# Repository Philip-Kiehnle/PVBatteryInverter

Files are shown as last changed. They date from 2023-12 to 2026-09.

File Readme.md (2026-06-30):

# PVBatteryInverter - Highly Efficient Photovoltaic and Battery Hybrid Inverter using GaN Semiconductors
This project was inspired by multiple drivers:
 * AC-connected battery systems have disadvantages in terms of charging efficiency ( PV -> DC/AC -> AC/DC -> Battery ) and cost/environmental impact, because of the additional inverter.  
 A multilevel battery converter is efficient but does not offer a DC port for PV and thus, increases installed converter power in the grid and grid operators have to calculate the worst case for grid utilization.
 * DC-connected battery systems do not guarantee a better efficiency by default. E.g. in case of a large inverter (~10 kW) operating under small loads during nighttime (30–150 Watt).
 * Commercial solutions often require an additional power meter for the self-consumption power control. In my opinion, this is a complete waste of time, space, resources and energy:
   * The installation is complicated, and requires space in the meter cabinet.
   * The additional power meter requires extra power of 0.4–2 Watt.
   * The additional power meter has an offset from the official meter measurement, meaning it cannot be used for exact zero-import control.
   * The digital energy meters in Germany already offer an optical interface, which can be set to send the actual power every second  [More details below](#head_electricityMeter)
 * GaN instead of SiC or Si-IGBT offers improved efficiency.
 * No GaN-based inverter is out there at the moment (9.12.2023)
 * Second-life 6 kWh battery was available
 * GaN full-bridge cells were available from another project
 * New west oriented PV plant has some shaded areas, which are directly connected to microinverter. But 8 PV-modules are unshaded most of the time and require a string inverter. A Hybrid (PV+Battery) Inverter for the unshaded PV-modules and a microinverter for the shaded PV-modules looks like the optimal solution.

Let's build an efficient 2kW hybrid inverter, which solves all the problems shown above!

System Overview:

System Overview

# Components

## PV Plant
```
8 x 405 W PV-modules in the string
STC:
Vmpp_module(25°C) = 36.48 V
Impp_module(25°C) = 11.10 A
Voc_module(25°C)  = 46.30 V

Temperature Coefficients of Voc = -0.28 %
Voc_module(-15°C)  = 51.49 V
Voc_string(-15°C)  = 411.9 V -> 650 V GaN semiconductors
```

## High-Voltage Battery
```
nunm_cells = 96
Vmin = 96 * 3.3 V = 316.8 V (grid feed-in is only possible when grid rms voltage is below 224 V or by using reactive power)
Vnom = 96 * 3.7 V = 355.2 V
Vmax = 96 * 4.2 V = 403.2 V
energy = 18 Ah * 355.2 V = 6.4 kWh
```

## Inverter Housing
An unused inverter housing was available, including passive components like boost inductors and an LCL-filter, which can be reused.

A control PCB and GaN Full-Bridge PCBs were added. This picture was taken during the development phase:

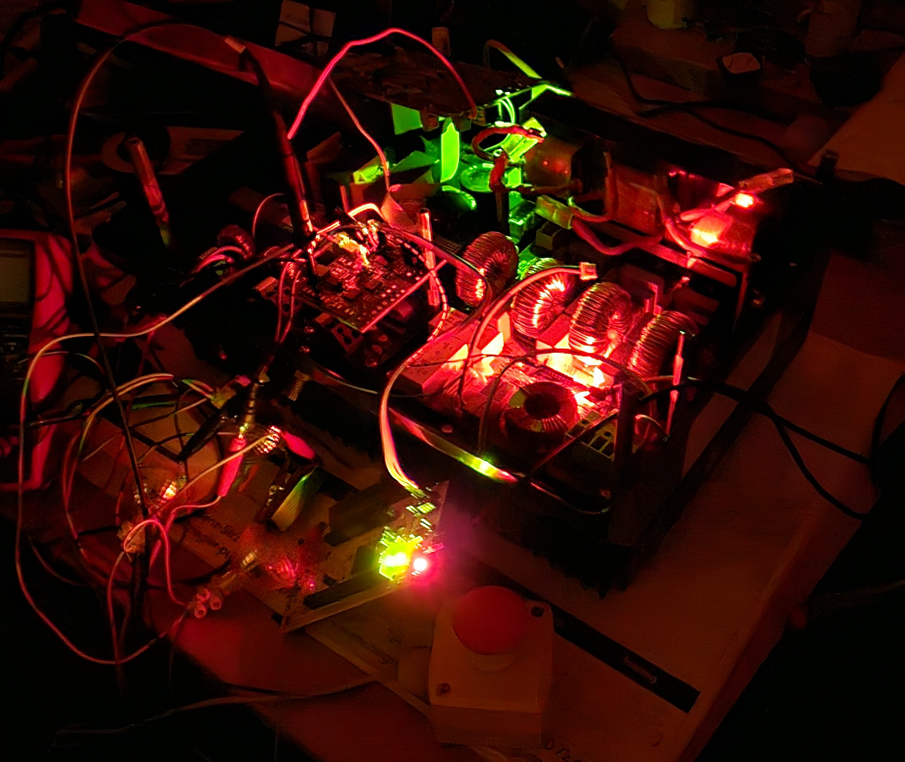
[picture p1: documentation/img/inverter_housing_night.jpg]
Inverter Housing


### PV input
Common-Mode-Choke (CMC) -> Capacitor: MKP 900V  12.5uF +-5% -> Inductor -> Diode for PV string protection during development -> GaN Half-Bridge

### LCL-Filter
Inverter side inductor: 1mH

### GaN Full-Bridge
```
GaN semiconductors:
Gan Systems GS66508B 650 V
Rds_on(25°C)  =  50 mOhm
Rds_on(112°C) = 100 mOhm

estimated loss:
I = 2000 W ÷ 230 V = 8.7 A
50 % conduction of low and high-side switch
Pcond(112°C) = 0.5*0.1 Ohm*(8.7 A)^2 = 3.8 W per switch

Switching loss (according to datasheet at Vds = 400 V, Ids = 15 A):
Eon=47.5 µJ
Eoff=8 µJ
Pswitch = 20 kHz * (47.5+8) µJ = 1.1 W
-> 4.9 W have to be dissipated for each transistor 

Thermal Model:
R_JC = 0.5 K/W (manufacturer)
R_PCB = 3.39 K/W
R_TIM = 0.28 K/W
R_HSA = 4.8 K/W
R= 8.97 K/W
Thermal interface material coefficient seems too optimistic -> use R=10K/W
With ambient 40°C and junction = 112°C each transistor can dissipate P=(112-40)/10=7.2W
This assumption has enough tolerance because:
  -operating junction temperature is 150°C and not 112°C
  -dissipated power will be lower than 7.2W

If the power rating is set to 2300 W, the loss will increase to:
Ploss = Pswitch + 0.5*0.1 Ohm*(10 A)^2 = 1.1 W + 5 W = 6.1 W
But the inverter's inductors had an original design power of 2 kW. On the other hand, the ripple is lower than in the original design, because of an increased switching frequency.
This increases the core loss but the central inductor of phase L2 can be assumed as a heat sink, because it is not used.

Start heatsink fan at 1200W (5.2A) assume 90mOhm:
Ploss = Pswitch + 0.5*0.09 Ohm*(5.2 A)^2 = 1.1 W + 1.2 W = 2.3 W
Minimum runtime is 30 sec, stop if power after timer runtime is lower than 1 kW. Restart timer if power > 1.2 kW during fan runtime.
```

### Control board [PVBatteryInverter_Mainboard](PVBatteryInverter_Mainboard)
An STM32G474 microcontroller is used to control the system.

#### Code Execution:

HRTIM 20 kHz controls Grid Full-Bridge
1. HRTIM period triggers ADC1
2. ADC1 DMA done calls ADC_ConvComplete with hadc1 instance
3. ADC2 for PV current is started (two ADCs simultaneously cause disturbance!)
4. AC control algorithm is executed and new dutycycle is set
5. 45 µs after ADC2 start, the 128 PV/DC current samples are acquired and ADC DMA calls ADC_ConvComplete with hadc2 instance
6. DC control algorithm is executed and new dutycycle is set. Exact timing not relevant for slow MPP-Tracker
7. wait for new ADC1 samples

## Energy Management System
Todo: opensource the git repo and add link

## Default Electricity Meter

The Iskra electricity meter offers a power resolution of 1 Watt and a temporal resolution of 1 second.  
Its permanent energy counting registers are written every 100 mWh.  
This equals to a power mismatch of 360 W for 1 second.  
So the controller has to avoid that, which is possible most of the time.  
In case of large load steps, like hobs switching with 2 kW, there will be a mismatch.  
But experiments have shown that for a cooking session of 30 minutes, a mismatch of about 12 Wh occurs.  
If this amount is equally spread over 24 hours, the mismatch in each hour is 0.5 W.
To beat that value, an additional energy meter must:
  * consume less than 0.5 W
  * offer better temporal resolution than 1 second
  * offer no offset compared to the main electricity meter, or use an offset in feed-in direction and thus always feeds a little bit of power into the grid
  * come at no cost

This demonstrates the whole extent of stupidity to install an additional energy meter, if a digital electricity meter is already installed!  
A detailed analysis is also carried out in the [PowerSensorEmulator
](https://github.com/Philip-Kiehnle/PowerSensorEmulator
) repository.

# Efficiency

## Power Consumption
Assuming 90 % efficiency of the 5 V power supply.

### Mode "Connected to AC Grid - Passive"
The gate signals are turned off whenever there is no exchange of AC power.

BMS: 6 W  
Smartphone: 1 W  
PV-Boost GaN Full-Bridge not switching: 5 V ⋅ 90 mA / 0.9 = 0.5 W  
Grid GaN Full-Bridge not switching: 5 V ⋅ 90 mA / 0.9 = 0.5 W  
Grid Relay: 0.4 W  
STM32_PVBatteryInverter PCB:  5 V ⋅ 50 mA / 0.9 = 0.28 W (todo: check)  
STM32_BatterySupervisor PCB:  5 V ⋅ 40 mA / 0.9 = 0.22 W (todo: check)  

**Total: 8.9 W**

### Mode "Idle"
BMS 12 V power supply is OFF, so the idle consumption is reduced to **2.9 W**.  
The BMS reactivation and the routine for closing contactors takes about 10 seconds.

### Mode "Connected to AC Grid - Active"
Todo: measure efficiency curve

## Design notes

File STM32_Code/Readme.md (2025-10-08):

# Howto

## Bootloader

In GCC preprocessor define USE_FULL_LL_DRIVER

Enter bootloader by pressing emergency stop and the reset button.  
In bootloader both LEDs (red and green) are lit.

```
philip@792G:~/Downloads/stm32flash-0.7$ ./stm32flash /dev/ttyUSB1 -b 115200
stm32flash 0.7

http://stm32flash.sourceforge.net/

Interface serial_posix: 115200 8E1
Version      : 0x31
Option 1     : 0x00
Option 2     : 0x00
Device ID    : 0x0469 (STM32G47xxx/48xxx)
- RAM        : Up to 96KiB  (16384b reserved by bootloader)
- Flash      : Up to 512KiB (size first sector: 1x2048)
- Option RAM : 48b
- System RAM : 28KiB

```

Write with verify and start application:
```
./stm32flash -b 115200 -w firmware.bin -v -g 0x8008000 -S 0x8008000 /dev/ttyUSB1
```
If process is interrupted, the booloader recovers after some minutes and the flash application can be restarted. 

Or flash via Android phone:
```
adb -e push 'STM32_PVBatteryInverter/Debug/STM32_PVBatteryInverter.bin' /data/local
adb -e shell
pkill log-
/data/local/stm32flash -b 115200 -w /data/local/STM32_PVBatteryInverter.bin  -v -g 0x8008000 -S 0x8008000 /dev/ttyUSB1
# A reset seems to be necessary after flash process. Direct start does not charge battery.
```

### Problems:
#### Data corruption can lead to execution of incomplete program
Todo: protect flash of bootloader and implement CRC (in bootloader seems more robust than in image. Bootloader should check CRC before starting the application.)

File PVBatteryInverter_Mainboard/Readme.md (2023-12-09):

# Aisler PCB made in Germany
minium amount: 3pcs  
area: 100mm*60mm = 60cm²  
```
Price Budget 2-Layer: 10€ + 3* 60*0.0525€/cm² = 19,45€ -> 23,15€
Price HD 2-Layer:     12€ + 3* 60*0.084€/cm²  = 27,12€ -> 32,27€
Price HD 4-Layer:     12€ + 3* 60*0.117€/cm²  = 33,06€ -> 39,34€
```

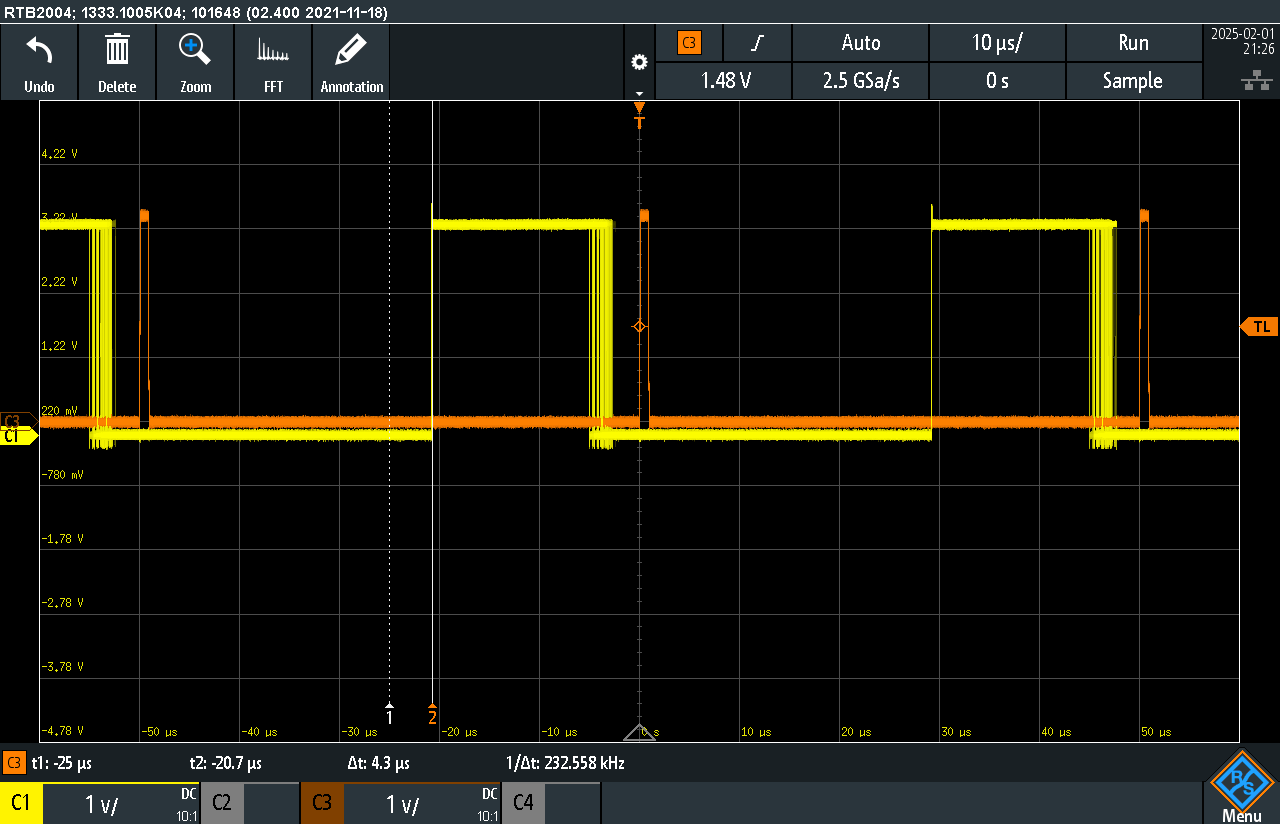
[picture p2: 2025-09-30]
documentation/img/4XOSR_ADC_delay.PNG

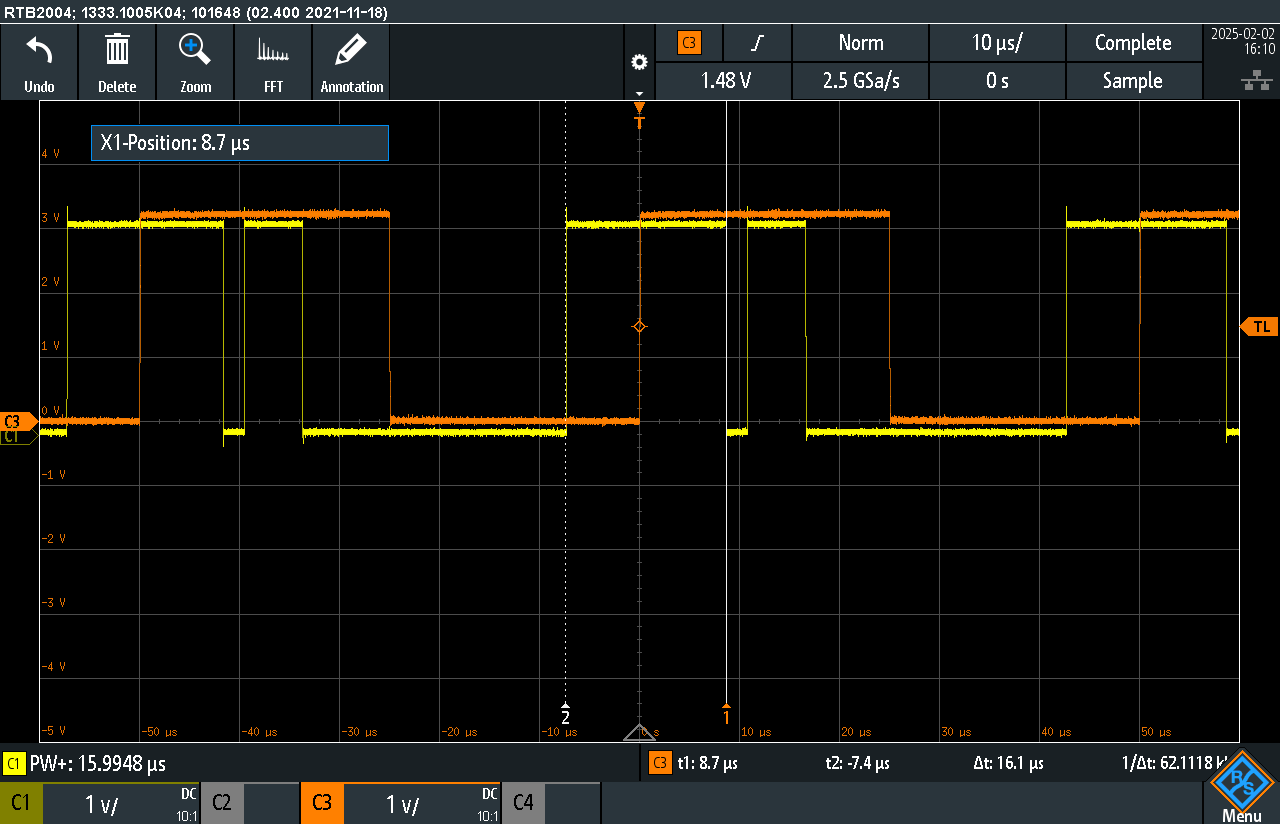
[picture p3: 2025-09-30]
documentation/img/2_phase_correct_ADC_trig_8xOSR_AC_ctrl.PNG

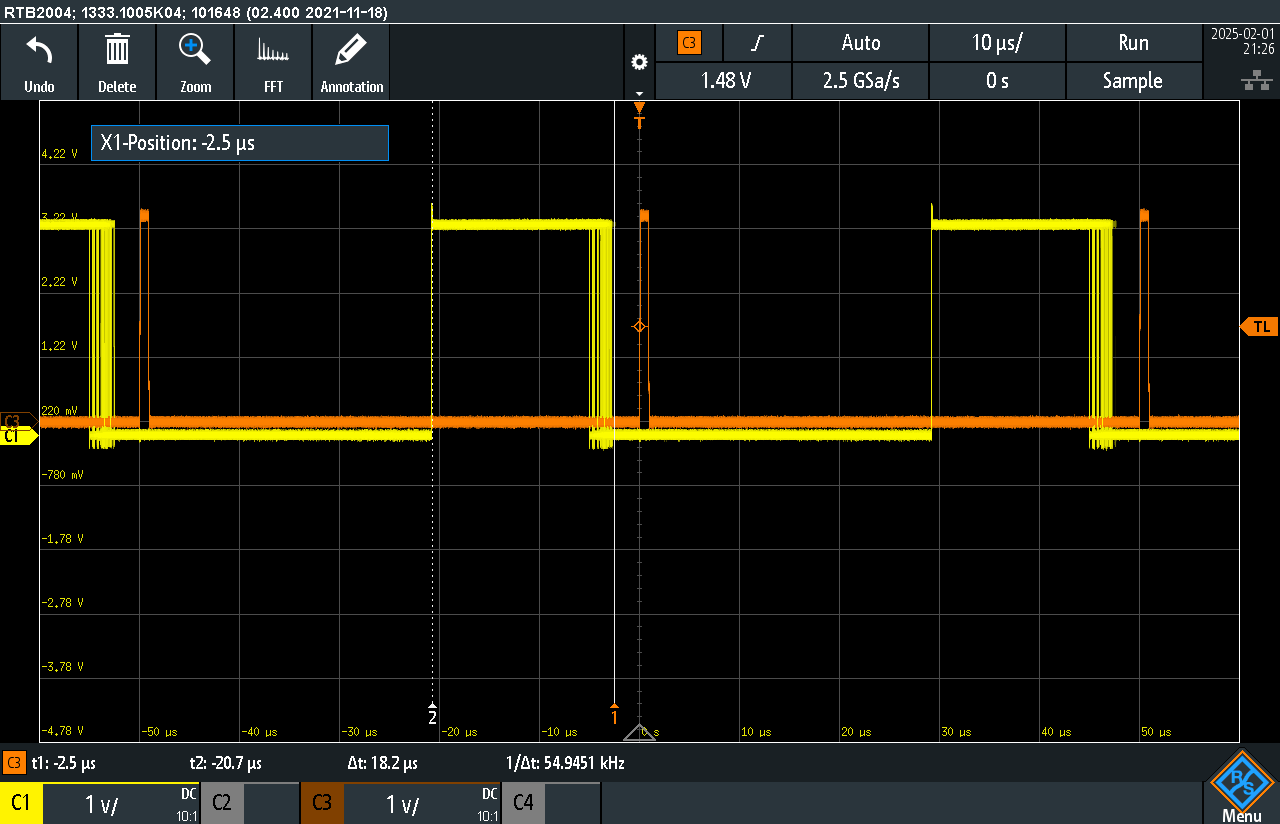
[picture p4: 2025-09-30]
documentation/img/4XOSR_ac_duty_calc_duration.PNG

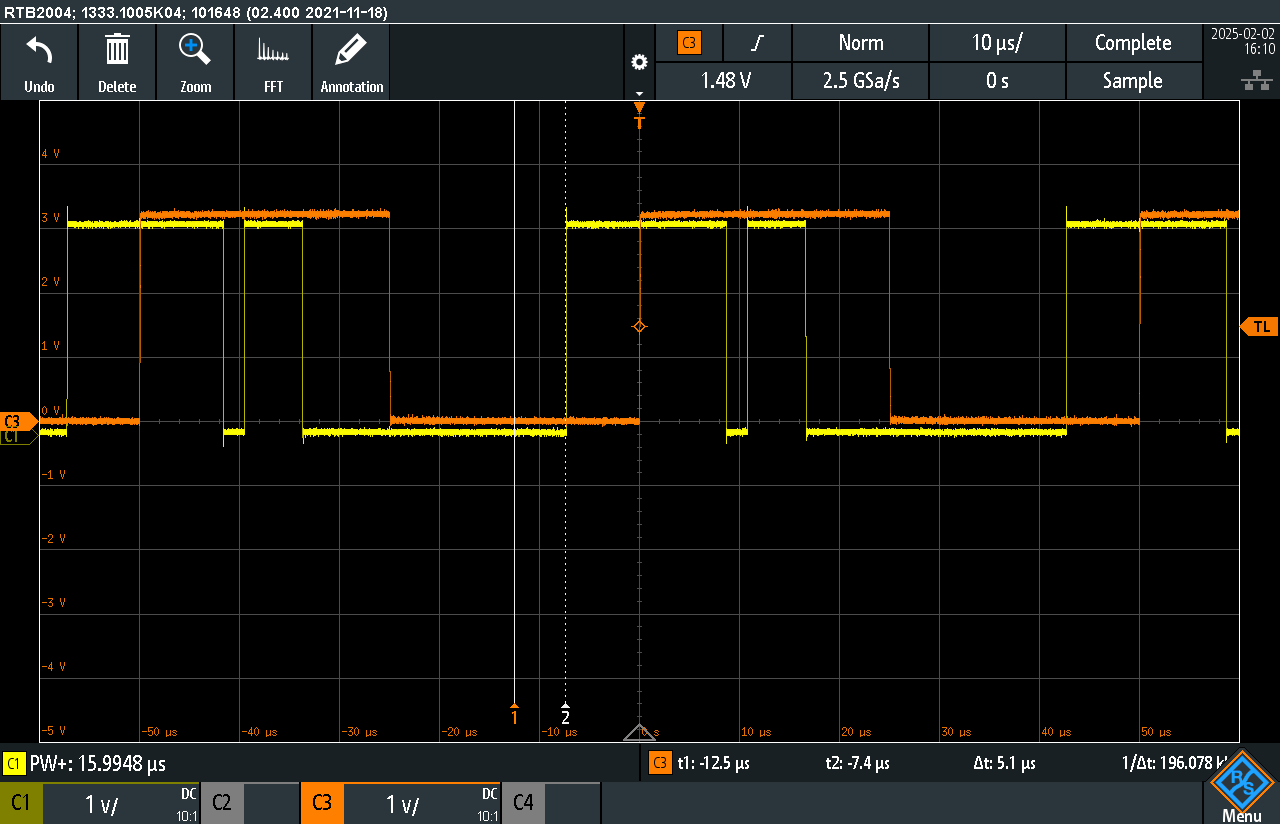
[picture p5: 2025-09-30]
documentation/img/1_phase_correct_ADC_trig_8xOSR_delay_until_ISR_start.PNG

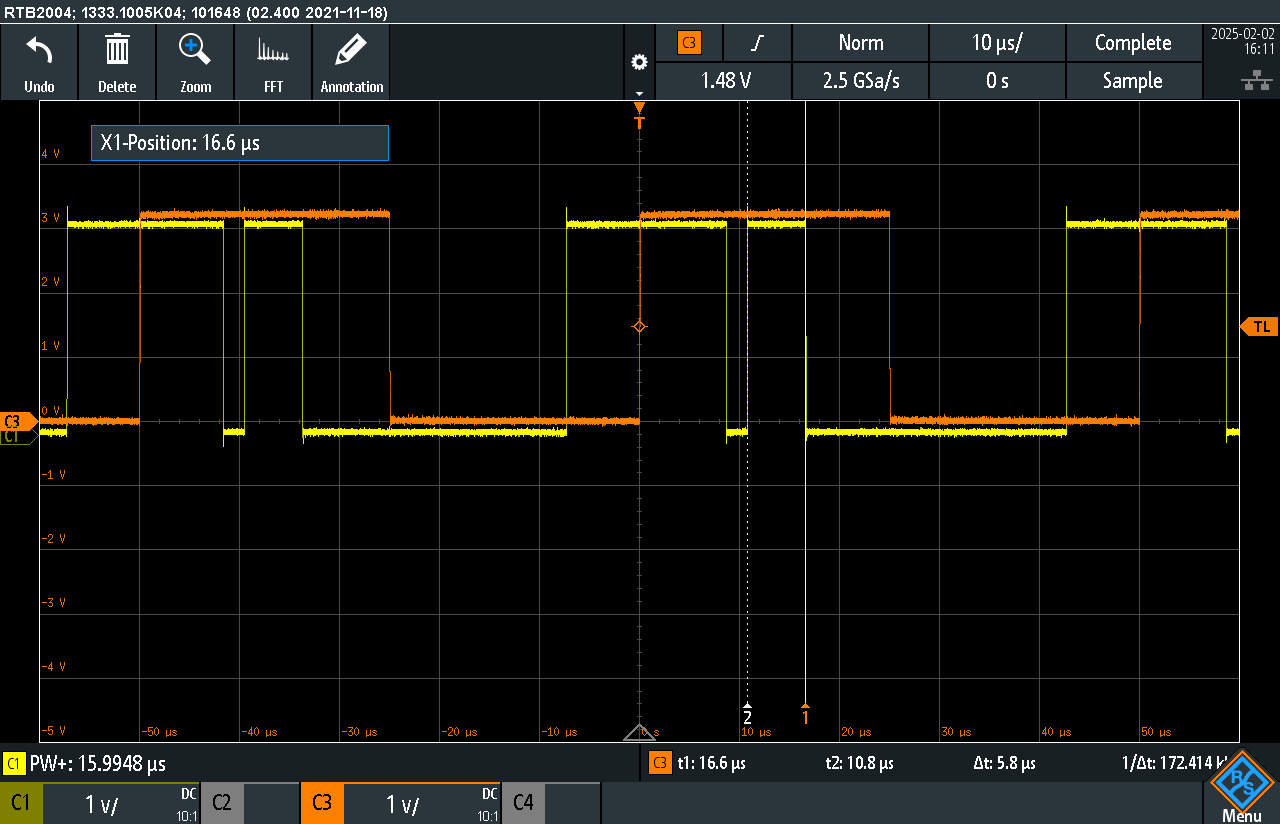
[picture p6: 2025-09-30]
documentation/img/4_phase_correct_ADC_trig_8xOSR_DC_ctrl.PNG

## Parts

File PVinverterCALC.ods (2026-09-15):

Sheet: Tabelle1
P | 75 | W
U | 230 | V
R | 705,333333333333 | Ohm
R | 400 | Ohm |  |  | 190 |  |  | 10,6 |  |  | 22
U | 38 | V |  | 450 |  |  | 33 |  |  | 33
I | 0,095 | A |  |  | 0,421286031042129 |  |  | 0,311764705882353 |  |  | 0,647058823529412
P | 3,61 | W |  | 1 |  |  | 1 |  |  | 1
Uin | 19 | V
Rin | 4,11 | Ohm |  | 20Watt | 7,2
I_short | 4,62 | A |  | 20Watt | 7,2
P_short | 87,83 | W |  | R | 5,6 |  | 35Watt | 4,11
 |  |  |  | 50Watt | 2,88
U0gan | 4,7 |  |  | R | 10
U0diode | 0,7 |  |  | R_ges | 32,88
Udrop | 5,4
U0 | 13,6 |  |  | P | 14,7201946472019
I0 | 0,37
Pgan | 1,73
P0 | 5,00
IDC_OFFSET_RAW | 2635
IDC_mV_per_LSB | 0,8056640625
IDC_mV_per_A | 35
IDC_RAW_TO_mA | 23,0189732142857
iDC_filt_raw | 2636
iDC_filt_mA | 23,0189732142857
DUTY_ABSMAX | 4250
VIN_MIN | 62
VIN_MAX | 320
VOUT_MIN | 288
VOUT_MAX | 384
DUTY_MIN | -472,222222222223
DUTY_MAX | 3563,80208333333
f | 20000
T | 0,00005
a | 4
C | 0,00078 | F
Tsigma | 0,00515
VR | 0,151456310679612
Tn | 0,0824
Kp_Vdc_real | 0,151456310679612
Ki_Vdc_real | 1,83806202281082
EXTEND_PI_VDC | 16
Kp_Vdc | 9925,84077669903
Ki_Vdc | 120459,23272693
c1 | 14041,5175213796
c2 | -14032,9997673478
ctrl->y += x * ctrl->c1 + ctrl->x_prev * ctrl->c2
x_prev | x | y | y_out
 | 0 | 0
0 | 100 | 1404151,75213796 | 21,4256553976128
100 | 100 | 1405003,52754113 | 21,4386524588186
 |  |  | fb boost
Vreal | corr boost | coor grid | vdc_filt50Hz | VdcFBboost_sinc | VdcFBgrid_sinc
33,2 | 33,220 | 33,246 | 33,5 | 33,5 | 33,7
33,18 |  |  | 33,5 | 33,7 | 33,7
33,18 |  |  | 33,5 | 34,4 | 33,7
33,1866666666667 |  |  | 33,5 |  | 33,7
avg_calib_corr |  |  | 0,990646766169154 |  | 0,984767556874382
45,65 | 45,615 | 45,578 | 46 | 46 | 46,2
45,66 |  |  | 46 | 46 | 46,2
45,67 |  |  | 46 | 46 | 46,2
45,66 |  |  | 46 |  | 46,2
 |  |  | 0,992608695652174 |  | 0,988311688311688
avg_calib_corr v1 |  |  | 0,991627730910664 |  | 0,986539622593035
VdcFBboost_sinc | 46,0
VdcFBgrid_sinc | 45,9
Vreal | 46,14
avg_calib_corr v2 |  |  | 1,00304347826087 |  | 1,00522875816993
calib |  |  | 0,994645728352566 |  | 0,991697999704628
 |  |  | theorey after calib |  |  |  | meas after calib
Vreal | vac_filt50Hz | error | after offset calib | after gain calib | error |  | Vreal | after calib | error
-50,48 | -50,200 |  |  |  |  |  | -50,64 | -50,5
-50,5 | -50,000 |  |  |  |  |  | -50,64 | -50,4
-50,51 | -50,200 |  |  |  |  |  | -50,63 | -50,4
-50,50 | -50,13 | 0,363 | -50,98 | -50,420 | 0,077 |  | -50,64 | -50,43 | 0,203
50,48 | 52 |  |  |  |  |  | 50,67 | 50,7
50,5 | 52 |  |  |  |  |  | 50,68 | 50,5
50,49 | 52 |  |  |  |  |  | 50,66 | 50,5
50,49 | 52,00 | 1,510 | 51,15 | 50,590 | 0,100 |  | 50,67 | 50,57 | -0,103
OFFSET | 0,933333333333351
V_AC_CALIB_OFFSET | 1976 | 3 | 1979
V_AC_CALIB_GAIN_PER_MIL | 989
VGRID_ADCR | 1157,1
ADC_BITS_VGRID | 12
vac_raw | 3,30377393523604 | 1
vac | 0,933300004995513 | 0,2824951171875
SigmaDelta software processing
single pulse edge counter
 |  |  |  | Vadc |  | edges
 |  |  |  | 0V |  | 250
 |  |  |  | 1V |  | 50
 |  |  |  | 1,25V |  | 0 | 1 in 256
Vcell |  | Vdc_max | divider | Vadc
4,25 | 96 | 408 | 0,002660 | 1,085 | 1,25 | 32,98
4,26 |  | 408,96 |  | 1,088 |  | 32,47
4,27 |  | 409,92 |  | 1,090 |  | 31,96
4,28 |  | 410,88 |  | 1,093 |  | 31,45
4,29 |  | 411,84 |  | 1,095 |  | 30,94
4,3 |  | 412,8 |  | 1,098 |  | 30,43
4,31 |  | 413,76 |  | 1,100 |  | 29,91
4,32 |  | 414,72 |  | 1,103 |  | 29,40
4,33 |  | 415,68 |  | 1,106 |  | 28,89
4,34 |  | 416,64 |  | 1,108 |  | 28,38
4,35 |  | 417,6 |  | 1,111 |  | 27,87
4,36 |  | 418,56 |  | 1,113 |  | 27,36
4,37 |  | 419,52 |  | 1,116 |  | 26,85
4,38 |  | 420,48 |  | 1,118 |  | 26,34
4,39 |  | 421,44 |  | 1,121 |  | 25,83
4,4 |  | 422,4 |  | 1,123 |  | 25,32
4,41 |  | 423,36 |  | 1,126 |  | 24,81

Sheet: Tabelle2
pll_set_phaseOffset((1<<15) * +10.0/20); // zero crossing of grid and converter voltage matched: +-1us
fgrid | 50 | Hz
R | 0,297 | Ohm
L | 0,00431 | Henry | 4,30765 | mH
ZL | 1,353 | Ohm
Z | 1,385 | Ohm
Contator OFF, Current feedforward OFF
Peak missmatch kurz nach max. Amplitude, max Verr=3,0V
Annahme: | Verr_max die ganze Zeit |  |  | realistisches Spannungsmittel über der Zeit
 | Verr | 3 | V | 2 | V
 | T_insgesamt | 1,1 | ms | 0,8 | ms
 | L | 0,002 | H | 0,002 | H
 | dI | 1,65 | A | 0,8 | A
-> kurzzeitiger Störstrom von ~1A durch nicht perfekt vorgesteuerte Netzspannung
-> Aber gut für das Netz, da damit Diodengleichrichter "ausgeglichen" werden
Contator OFF, Current feedforward ON
With I_AMP_MAX = 3,0A, Z=1,385
converter voltage leading 0,30-0324ms
Vgrid_amp | 44,53 | V
Vinv_amp | 45,61 | V
-> Vgrid_amp nur niedriger, weil Spitze abgeflacht
Vgrid_amp | -44,63 | V | -0,100000000000001
Vinv_amp | -45,61 | V | 0 | -> Spannung ist symmetrisch, Calibration hat funktioniert
Differenzspannung zwischen Netz und Inverter ca. 5,4ms = ~90° vor Netzspannung
-> Todo, nachrechnen ob die Phasenverschiebung passt

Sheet: system model
Amprobe SM-550-EUR for current measurement
UNI-T UT210E for voltage measurement
fgrid | 50 | Hz
Main Inductor
L | 2 | mH
V | 19,7 | 19,8 | 29,8 | mV
I | 293,9 | 293,8 | 441,4 | mA
R | 0,0670 | 0,0674 | 0,0675 | Ohm
R | 0,0673
Inductor 3 connection point to L3 including short N wire |  |  |  |  |  |  | Inductor 1 connection point to L1 including short L wire
V | 28,7 | 29 | 42,1 | mV | 27,7 |  | 29,2 | 28,8 | 45,1
I | 307,5 | 308 | 444 | mA | 295,5 |  | 294 | 293,6 | 448,2
R | 0,0933 | 0,0942 | 0,0948 | Ohm | 0,0937 |  | 0,0993 | 0,0981 | 0,1006
R | 0,0941 |  |  |  |  |  | 0,0993
R_out | 0,0967
L_LCL2 | 1,1 | mH without Common mode choke
Trafo | zwei serielle Windungssysteme + 5 extra Windungen mit Lüsterklemme
V | 60,6 | 92,6 | 92,4 | mV
I | 288,7 | 441,5 | 440,7 | mA
R | 0,2099 | 0,2097 | 0,2097 | Ohm
R | 0,2098
L | 30,0 | uH | 20-44uH gemessen mit rp-ims python tool am Oszi
Kupfer spez. Widerstand
 | 0,01678 | Elektrischer Widerstand Ohm mm²/m (bei 20°C)
1,5mm² | 0,01119 | Ohm/m
16mm² | 0,00105 | Ohm/m
ESR 390uF 550V ELko
340 | mΩ | 100 | Hz | 20 | °C
R_capacitor | 0 | mΩ | part of dutycycle feedback loop
Rtrack | 2 | mΩ
R_GaN | 200 | mΩ
Rtrack | 4 | mΩ
R_1u2H | 7,3 | mΩ
Rwire | 3,4 | mΩ | 15 | cm einfache Länge
R_mainL | 200,0 | mΩ
R_out | 280,5 | mΩ
R_relais | 0,1 | mΩ | Kontaktwiderstand von zwei ebenen Kupferscheiben mit D=1mm, die mit der Kraft 2,7 N aneinander gepresst werden
R_connector | 0,5 | mΩ
R_wire | 30,2 | mΩ | 135 | cm einfache Länge
R_trafo | 209,8 | mΩ | zwei serielle Windungssysteme + 5 extra Windungen
R_trafo prim | 3,4 | mΩ | 15 | m Drahtwickel | geschätzt
R_grid | 11,8 | mΩ | 7 | Winding Ratio
Rsum | 697,8 | mΩ
R_wireInHouse | 335,6 | mΩ | 15 | m einfache Länge
R_circuit_breaker | 8,5 | mΩ | ABB S200 16A B
R_fuse | 3,0 | mΩ | 35A DIIIGG50V35 |  | R_SLS_Switch | 4,6 | mΩ | Hager HTN335E
R_NHfuse | 1,2 | mΩ | 63A L223685 |  |  | 2,6 | mΩ | 35A H223682
R_wireInStreet | 209,8 | mΩ | 100 | m einfache Länge
R_MVtrafo | 20,0 | mΩ
L_track | 0,002 | mH
L_1u2H | 0,0024 | mH
L_main | 4,573 | mH
L_LCL2 | 5,614 | mH | L_LCL2 hat 496mV Spannungsabfall bei 50Hz aber L_main nur 404mV → L2 ist größer todo: warum mit rp-ims nur 1mH gemessen?
L_CMC_diff | 0,008 | mH | differential Mode inductance |  | estimated
L_wire | 0,004 | mH | Netzspannungsmessung ist Teil der feedback loop, daher ohne Berücksichtigung
L_trafo | 0,03 | mH
L_trafo_prim | 0,02 | mH | geschätzt
L_grid | 0,1 | mH | geschätzt
L_sum | 10,200 | mH |  | Ziel 10,2
R_old | 397 | mOhm | 2xGaN + 2 x large choke + 2xsmall choke + transformer
L_old | 4,308 | mHenry | 2 x large choke + 2xsmall choke (todo check 150uH) + transformer
gamma | 73,65 | °
Rsum | 697,8 | mΩ
L_sum | 10,200 | mH
R_factor | 1,76
L_factor | 2,37
Z_factor | 2,33
gamma_new | 77,72 | °
shift | 0,225834058765433 | ms
Rsum | 882,0 | mΩ | mod for more current, did not work but shifted current in phase
L_sum | 10,200 | mH
R_factor | 1,2641
L_factor | 1,00
Z_factor | 1,26
gamma_new | 74,61 | °
shift | -0,172502827052372 | ms

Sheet: PR_controller
R | 0,7 | Ohm
L | 0,00102 | Henry | 0,1 | saturation
f | 20000 | Hz
TA | 0,00005 | s
w0 | 314,16
wc | 6,28
Tsigma | 0,0001016 | s | 2 | *TA
Kp | 5,02
Ki | 3444,88
pow(TA*w0,2) | 0,000246740110027233
denom | 4,00150337717146
extend_bits | 14
int cx[3] = { (Kp + (4*Ki*TA*wc)/(pow(TA*w0,2) + 4*wc*TA + 4)), (2*Kp - (16*Kp + 8*Kp*TA*wc)/(pow(TA*w0,2) + 4*wc*TA + 4)), Kp - (4*Ki*TA*wc + 8*Kp*TA*wc)/(pow(TA*w0,2) + 4*wc*TA + 4) };
Cx[0] | 6,10152000161034 | 5,02 | 1,08183496224026 |  | 99967
Cx[1] | -10,0349792102555 | 10,0393700787402 | 20,0743492889957 |  | -164413
Cx[2] | 3,93469730095415 | 5,02 | 1,08498773841593 |  | 64466
Cy[0] | 1,99912527012149 |  | 1,99912527012149 |  | 32754
Cy[1] | -0,999371917530494 | 1 | 1,99937191753049 |  | -16374
iref | i | x | y
1 | 0 | 1 | 0
1 | 0 | 1 | 0
1 | 0 | 100 | 604,05
1 | 0 | 100 | -19885412,50
V2
https://imperix.com/doc/implementation/proportional-resonant-controller
a1 | 4,32896625494657 |  |  |  | 70926
b0 | 4,00150337717146 |  |  |  | 65561
b1 | -7,99950651977995 |  |  |  | -131064
b2 | 3,99899010304859 |  |  |  | 65519
iref | i | x | y
1 | 0 | 1 | 0
1 | 0 | 1 | 0
1 | 0 | 100 | 107,10
1 | 0 | 100 | 4,02

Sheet: power_controller
Kp | 0,5
Ki | 0,4545
T | 1
c1 | 0,7273
c2 | -0,2727
p_ac_low_power_mode_enter | 90 | W
p_ac_low_power_mode_exit | 160 | W
V1 compensation of one direction |  |  |  |  |  |  |  | V2 feedin before switchoff
problem: | at exact power, second switchoff may take long (90W/180W at p_load=90W)
 | Tustin |  |  | Turnoff criterion | inverter on | Ws in meter | grid consumption |  | Tustin |  |  | Turnoff criterion | inverter on | Ws in meter | forward euler?
load | x (p_pcc) | y |  |  |  |  |  | load | x (p_pcc) | y |  |  |  |  | x | I | y
90 | 10 | 40 |  | 1 | 1 | 0 | 0 | 50 | 10 | 40 |  | 1 | 1 | 0 | 10 | 40 | 50
90 | 50 | 73,6 | 34 | 1 | 0 | 50 | 0 | 50 | 10,0 | 44,5 | 4,5 | 0 | 0 | 10 | 50 | 62,7272727272728 | 87,7272727272728 | 37,7272727272728
90 | 90 | 125,5 | 52 | 0 | 0 | 140 | 0 | 50 | 50,0 | 78,2 | 33,6 | 0 | 0 | 60 | 50 | 85,4545454545455 | 110,454545454546 | 22,7272727272727
90 | 90 | 166,4 | 41 | 0 | 1 | 230 | 0 | 50 | 50,0 | 100,9 | 22,7 | 0 | 0 | 110 | 50 | 108,181818181818 | 133,181818181818 | 22,7272727272727
90 | -76 | 86,3 | -80 | 1 | 1 | 154 | 0 | 50 | 50,0 | 123,6 | 22,7 | 0 | 0 | 160 | 50 | 130,909090909091 | 155,909090909091 | 22,7272727272727
90 | 4 | 109,8 | 24 | 0 | 0 | 157 | 0 | 50 | 50,0 | 146,4 | 22,7 | 0 | 1 | 210
90 | 90 | 174,3 | 64 | 0 | 1 | 247 | 0 | 50 | -96,4 | 62,6 | -83,7 | 1 | 1 | 113,636363636364
90 | -84 | 88,4 | -86 | 1 | 1 | 163 | 0 | 50 | -12,6 | 79,7 | 17,1 | 0 | 1 | 101,0
90 | 2 | 112,6 | 24 | 0 | 0 | 165 | 0 | 50 | -29,7 | 61,6 | -18,2 | 1 | 1 | 71,3
90 | 90 | 177,6 | 65 | 0 | 1 | 255 | 0 | 50 | -11,6 | 61,3 | -0,3 | 1 | 1 | 59,7
90 | -88 | 89,3 | -88 | 1 | 1 | 167 | 0 | 50 | -11,3 | 56,2 | -5,0 | 1 | 1 | 48,4
90 | 1 | 113,7 | 24 | 0 | 0 | 168 | 0 | 50 | -6,2 | 54,8 | -1,5 | 1 | 1 | 42,2
90 | 90 | 179,0 | 65 | 0 | 1 | 258 | 0 | 50 | -4,8 | 53,0 | -1,8 | 1 | 1 | 37,5
90 | -89 | 89,7 | -89 | 1 | 1 | 169 | 0 | 50 | -3,0 | 52,1 | -0,9 | 1 | 1 | 34,5
90 | 0 | 114,2 | 24 | 0 | 0 | 169 | 0 | 50 | -2,1 | 51,4 | -0,7 | 1 | 1 | 32,3
90 | 90 | 179,6 | 65 | 0 | 1 | 259 | 0 | 50 | -1,4 | 51,0 | -0,4 | 1 | 1 | 30,9
90 | -90 | 89,9 | -90 | 1 | 1 | 169 | 0
90 | 0 | 114,4 | 25 | 0 | 0 | 170 | 0
90 | 90 | 179,8 | 65 | 0 | 1 | 260 | 0
90 | -90 | 90,0 | -90 | 1 | 1 | 170 | 0
90 | 0 | 114,5 | 25 | 0 | 0 | 170 | 0
90 | 90 | 179,9 | 65 | 0 | 1 | 260 | 0
90 | -90 | 90,0 | -90 | 1 | 1 | 170 | 0
90 | 0 | 114,5 | 25 | 0 | 0 | 170 | 0
90 | 90 | 180,0 | 65 | 0 | 1 | 260 | 0
90 | -90 | 90,0 | -90 | 1 | 1 | 170 | 0
2340 | 180,0 | 2170,0

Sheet: Efficiency
 |  |  |  |  |  |  |  | No objective argument for efficiency calculation! |  | AC-Cable Single-Phase Efficiency
Time | P_inverter_bat |  |  | Time | P_bat |  |  | n | n average | Copper Resistivity | 0,01750 | Ω⋅mm²/m | at 20 °C
2024-02-18 | 23:37:15 | -75 | W | 2024-02-18 | 23:37:15 | -84 | W | 89,3 % |  | Temperature coefficient | 0,00393 | 1/K
2024-02-18 | 23:37:21 | -82 | W | 2024-02-18 | 23:37:21 | -90 | W | 91,1 %
2024-02-18 | 23:37:31 | -77 | W | 2024-02-18 | 23:37:31 | -83 | W | 92,8 % |  | Copper Resistivity | 0,01784 | Ω⋅mm²/m | at 25 °C
2024-02-18 | 23:37:39 | -75 | W | 2024-02-18 | 23:37:39 | -91 | W | 82,4 %
2024-02-18 | 23:37:48 | -89 | W | 2024-02-18 | 23:37:48 | -107 | W | 83,2 % |  | Voltage | 230 | V
2024-02-18 | 23:37:57 | -79 | W | 2024-02-18 | 23:37:57 | -88 | W | 89,8 % |  | Cross-Section | 1,5 | mm² | 2,5 | mm²
2024-02-18 | 23:38:01 | -82 | W | 2024-02-18 | 23:38:01 | -92 | W | 89,1 % |  | Copper Resistance per meter | 0,01190 | Ω/m | 0,00714 | Ω/m
2024-02-18 | 23:38:06 | -92 | W | 2024-02-18 | 23:38:06 | -107 | W | 86,0 %
2024-02-18 | 23:38:11 | -84 | W | 2024-02-18 | 23:38:11 | -89 | W | 94,4 % |  | Power | 1600 | W
2024-02-18 | 23:38:15 | -92 | W | 2024-02-18 | 23:38:15 | -111 | W | 82,9 % |  | Current | 6,96 | A
2024-02-18 | 23:38:22 | -86 | W | 2024-02-18 | 23:38:22 | -94 | W | 91,5 %
2024-02-18 | 23:38:30 | -76 | W | 2024-02-18 | 23:38:30 | -82 | W | 92,7 % |  | Cable Length | 10 | m | 10 | m
2024-02-18 | 23:38:53 | -82 | W | 2024-02-18 | 23:38:53 | -92 | W | 89,1 % |  | Cable Fwd and Return Length | 20 | m | 20 | m
2024-02-18 | 23:39:07 | -79 | W | 2024-02-18 | 23:39:07 | -95 | W | 83,2 % |  | Cable Loss | 11,5 | W | 6,9 | W
2024-02-18 | 23:39:10 | -80 | W | 2024-02-18 | 23:39:10 | -90 | W | 88,9 % |  | Cable Efficiency | 99,28 % |  | 99,57 %
2024-02-18 | 23:39:13 | -77 | W | 2024-02-18 | 23:39:13 | -90 | W | 85,6 %
2024-02-18 | 23:39:16 | -81 | W | 2024-02-18 | 23:39:16 | -90 | W | 90,0 %
2024-02-18 | 23:39:19 | -79 | W | 2024-02-18 | 23:39:19 | -87 | W | 90,8 %
2024-02-18 | 23:39:23 | -77 | W | 2024-02-18 | 23:39:23 | -88 | W | 87,5 %
2024-02-18 | 23:39:26 | -82 | W | 2024-02-18 | 23:39:26 | -104 | W | 78,8 %
2024-02-18 | 23:39:29 | -80 | W | 2024-02-18 | 23:39:29 | -104 | W | 76,9 %
2024-02-18 | 23:39:37 | -81 | W | 2024-02-18 | 23:39:37 | -86 | W | 94,2 %
2024-02-18 | 23:39:42 | -82 | W | 2024-02-18 | 23:39:42 | -90 | W | 91,1 %
2024-02-18 | 23:39:46 | -82 | W | 2024-02-18 | 23:39:46 | -97 | W | 84,5 %
2024-02-18 | 23:39:50 | -76 | W | 2024-02-18 | 23:39:50 | -76 | W | 100,0 %
2024-02-18 | 23:39:55 | -81 | W | 2024-02-18 | 23:39:55 | -88 | W | 92,0 %
2024-02-18 | 23:40:18 | -73 | W | 2024-02-18 | 23:40:18 | -74 | W | 98,6 % | 88,8 %
2024-02-18 | 23:40:32 | -113 | W | 2024-02-18 | 23:40:32 | -129 | W | 87,6 %
2024-02-18 | 23:40:45 | -112 | W | 2024-02-18 | 23:40:45 | -127 | W | 88,2 %
2024-02-18 | 23:40:48 | -111 | W | 2024-02-18 | 23:40:48 | -126 | W | 88,1 %
2024-02-18 | 23:40:51 | -109 | W | 2024-02-18 | 23:40:51 | -124 | W | 87,9 %
2024-02-18 | 23:40:54 | -109 | W | 2024-02-18 | 23:40:54 | -123 | W | 88,6 %
2024-02-18 | 23:41:06 | -107 | W | 2024-02-18 | 23:41:06 | -119 | W | 89,9 %
2024-02-18 | 23:41:10 | -107 | W | 2024-02-18 | 23:41:10 | -119 | W | 89,9 %
2024-02-18 | 23:41:14 | -107 | W | 2024-02-18 | 23:41:14 | -121 | W | 88,4 %
2024-02-18 | 23:41:18 | -108 | W | 2024-02-18 | 23:41:18 | -122 | W | 88,5 %
2024-02-18 | 23:41:22 | -107 | W | 2024-02-18 | 23:41:22 | -120 | W | 89,2 %
2024-02-18 | 23:41:26 | -106 | W | 2024-02-18 | 23:41:26 | -119 | W | 89,1 %
2024-02-18 | 23:41:50 | -107 | W | 2024-02-18 | 23:41:50 | -120 | W | 89,2 %
2024-02-18 | 23:41:59 | -106 | W | 2024-02-18 | 23:41:59 | -119 | W | 89,1 % | 88,7 %

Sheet: DCDC-Converter
Vin | 36 | V
Vout | 50 | V
L | 500 | uH | ??
freq | 20 | kHz
duty_HS | 0,72
I_rip | 1,008 | A
I_lück | 0,504 | A
 | Single-Phase mod |  |  | Original 3 Phase
n | 8
Vmodule | 36 | V
Vin | 288 | V |  | 325 | V
Vout | 384 | V |  | 650 | V
f | 20 | kHz |  | 20 | kHz
L | 2 | mH |  | 2 | mH
duty | 0,25 |  |  | 0,50
dI | 1,80 | A |  | 4,06 | A
dI | 1,80 | A |  | 4,06 | A
Inom | 9 | A |  | 9 | A
Ripple | 20 % |  |  | 45 %

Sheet: 5V_undervoltageDetection
Prevent GaN not beeing switched off safely, in case 5V supply drops. Gatedriver has 3V Undervoltage lockout, which is not sufficient in the used zener diode circuit for 6V / -3V.
-> Use microcontroller comparator to detect drop in 5V supply.
Vsupply,min | 4,5 | V | for DC-DC converter, if Gatedriver looses 0.5V*9V/5V=0.9V, negative turnoff is reduced to -2.1V. Turnon stays at 6V
Vrefint,min | 1,19 | V
Vrefint,max | 1,23
 | R in kOhm | Volt |  | R in kOhm | Volt | Lowpass
Vtrigger |  | 4,511 |  |  | 4,663
R1 | 120 |  |  | 120
 |  | 1,19 |  |  | 1,23
R2 | 43 |  |  | 43
 |  | 0 |  |  | 0 | C | 1 | nF
 |  |  |  |  |  | fg | 5028 | Hz
 | R in kOhm |  |  | R in kOhm
Vtrigger |  | 4,804 |  |  | 4,966
R1 | 82 |  |  | 82
 |  | 1,19 |  |  | 1,23
R2 | 27 |  |  | 27
 |  | 0 |  |  | 0
Test:
4,69 and 4,67V does not trigger
4,65V triggers comparator

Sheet: loaded_lowpass
Formel1: |  |  |  |  | Todo: prüfen ob 18nF verbaut |  |  | Welcher Kondensator ist in FB grid verbaut?
 | original |  | mod: GaN_FB PV boost |  | mod: GaN_FB grid |  |  | Messung bei 10kHz ohne 375kOhm Spannungsteiler
R1 | 600 | kOhm | 375 | kOhm | 375 | kOhm |  |  | laut LTspice |  | laut Oszi
R2 | 1 | kOhm | 1 | kOhm | 1 | kOhm | PCB | C in nF | Dämpfung db | Phase | Dämpfung db | Phase | Ampl. Ratio | delay (us)
 |  |  |  |  |  |  | GaN_FB PV grid? | 18 | -5 | -56 | -2,87 | -19,1 | 0,719 | 5,3
R3 | 1,36 | kOhm | 1,36 | kOhm | 1,36 | kOhm | GaN_FB PV boost | 100 | -18 | -83 | -5,75 | -7,0 | 0,516 | 1,95 | Mehr Dämpfung aber weniger Phasenverschiebung?!
 |  |  |  |  |  |  |  | 10 | -2,38 | -40
Rref | 2,351 | kOhm | 2,345 | kOhm | 2,345 | kOhm
C | 100 | nF | 100 | nF | 18 | nF
fg | 677,0 | Hz | 678,6 | Hz | 3770,2 | Hz
Todo: Formel1 korrekt?, laut LTspice Ja
Todo: Formel2 korrekt?, laut LTspice Ja für letzten Fall mit 3.75kHz besser
Todo: ordentliche Herleitung
Formel2:
R1 | 600 | kOhm | 375 | kOhm | 375 | kOhm
R2 | 1 | kOhm | 1 | kOhm | 1 | kOhm
R3 | 1,36 | kOhm | 1,36 | kOhm | 1,36 | kOhm
Rref | 2,358 | kOhm | 2,357 | kOhm | 2,357 | kOhm
C | 100 | nF | 100 | nF | 18 | nF
fg | 674,9 | Hz | 675,1 | Hz | 3750,8 | Hz

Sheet: LCL-filter
fgrid | 50
fsw | 20000 | Hz | 20 | kHz
Lf | 0,002 | H | 2000 | uH
Lg_discrete | 0,003 | H | 3000 | uH
Lg_CMC | 0,000003 | H | 3 | uH
Lg_grid | 0,00005 | H | 50 | uH
Lgrid | 0,003053 | H | 3053 | uH
Cf | 0,0000011 | F | 1,1 | uF
Rf | 0 | Ohm
1. Keep resonant frequency between 10*fgrid and 0.5*fswitch
10*fgrid | 500 | Hz | 0,5 | kHz
fres | 4365 | Hz | 4,4 | kHz
0,5*fsw | 10000 | Hz | 10 | kHz
2. Reduce total L in order to reduce voltage drop. This increases Cf.
3. Cf should be reduced in order to reduce VAr and increase efficiency.
4. Reduce damping resistors to increase efficiency. Todo: Check if parallel Cf path with 10*Cf and R helps. 10-50% of Cf impedance
5. Be compliant with norm IEEE-519-2014

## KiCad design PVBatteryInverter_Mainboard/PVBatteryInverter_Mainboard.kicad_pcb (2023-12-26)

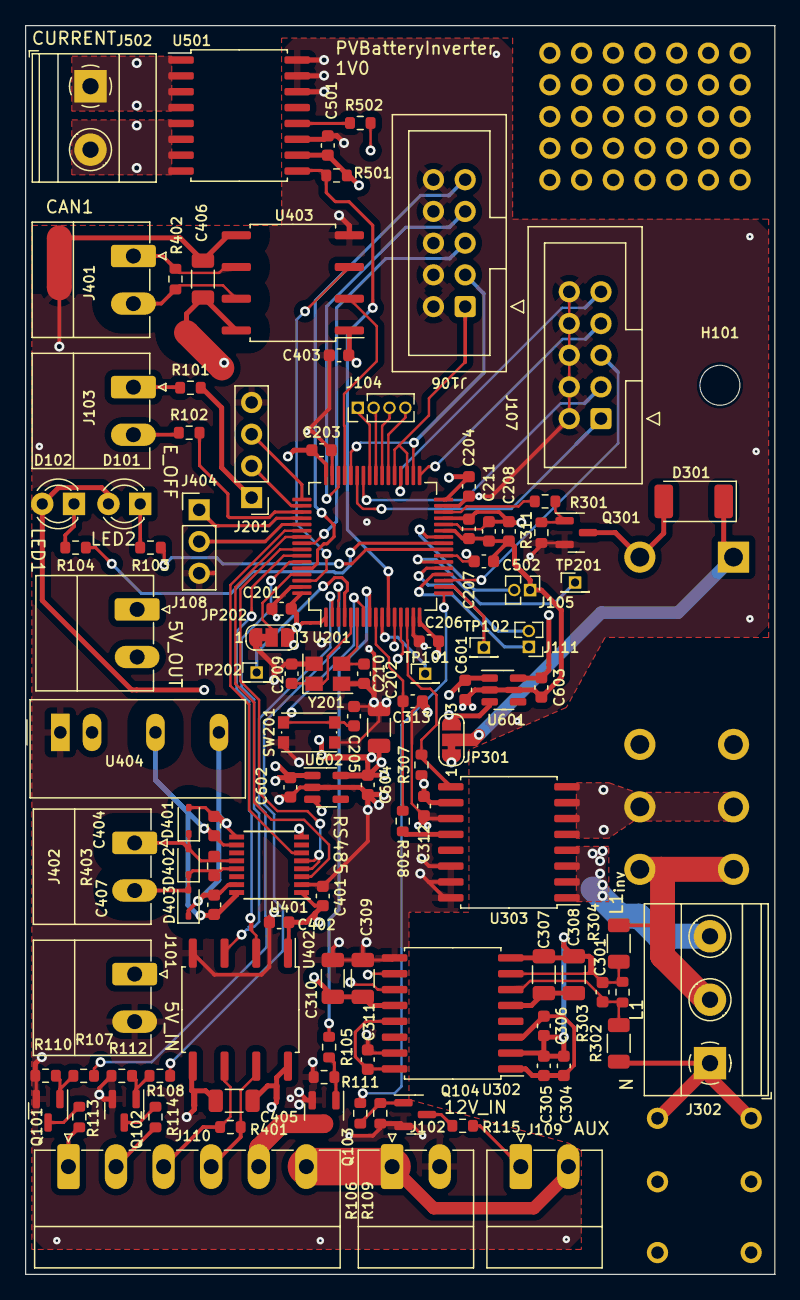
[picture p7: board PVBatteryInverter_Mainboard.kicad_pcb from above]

Board: 4 copper layers, 60.0 x 100.0 mm, 116 parts (1 on the bottom side), 100 nets.

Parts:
C201, C203, C204, C205, C206, C211, C306, C311, C312, C401, C402, C403, C404, C407, C501: 100n; C_0603_1608Metric
C202: 4u7; C_1206_3216Metric
C207: 10n; C_0603_1608Metric
C208, C304: 1u; C_0603_1608Metric
C209, C210, C301: 10p; C_0603_1608Metric
C305: 1n; C_0603_1608Metric
C307, C405, C406: 100n; C_1206_3216Metric
C308, C309: 1n; C_1206_3216Metric
C310: 1µ; C_1206_3216Metric
C313, C502: 2n2; C_0603_1608Metric
C601, C602, C603, C604: 1µ; C_0603_1608Metric
D101, D102: LED; LED_D3.0mm
D301: US1D 200V 1A 50ns Silizium SMA; D_MELF
D401, D402, D403: D_TVS; D_SOD-323
H101: MountingHole; MountingHole_3.2mm_M3
J101: 5V_IN; PhoenixContact_MC_1,5_2-G-3.81_1x02_P3.81mm_Horizontal
J102: 12V_IN; PhoenixContact_MC_1,5_2-G-3.81_1x02_P3.81mm_Horizontal
J103: EMERGENY_OFF; PhoenixContact_MC_1,5_2-G-3.81_1x02_P3.81mm_Horizontal
J104: TIM; PinHeader_1x04_P1.27mm_Vertical
J105: ADC2_12; PinHeader_1x02_P1.27mm_Vertical
J106: FB_Boost; IDC-Header_2x05_P2.54mm_Vertical
J107: FB_Grid; IDC-Header_2x05_P2.54mm_Vertical
J108: 5V_OUT; PhoenixContact_MC_1,5_2-G-3.81_1x02_P3.81mm_Horizontal
J109: AUX_OpenDrain; PhoenixContact_MC_1,5_2-G-3.81_1x02_P3.81mm_Horizontal
J110: BMS; PhoenixContact_MC_1,5_6-G-3.81_1x06_P3.81mm_Horizontal
J111: ADC2_3-4; PinHeader_1x02_P1.27mm_Vertical
J201: SW_DBG; PinHeader_1x04_P2.54mm_Vertical
J302: 230V; TerminalBlock_Phoenix_MKDS-1,5-3-5.08_1x03_P5.08mm_Horizont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
J401: CAN1; PhoenixContact_MC_1,5_2-G-3.81_1x02_P3.81mm_Horizontal
J402: RS485; PhoenixContact_MC_1,5_2-G-3.81_1x02_P3.81mm_Horizontal
J404: UART; PinHeader_1x03_P2.54mm_Vertical
J502: Current sense; TerminalBlock_Phoenix_MKDS-1,5-2-5.08_1x02_P5.08mm_Horizont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
JP202: BOOT_MODE; SolderJumper-3_P1.3mm_Bridged12_RoundedPad1.0x1.5mm_NumberL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
JP301: SolderJumper_3_Bridged12; SolderJumper-3_P1.3mm_Bridged12_RoundedPad1.0x1.5mm_NumberL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
NT301, NT403, NT404: NetTie_2; NetTie-2_SMD_Pad0.5mm
NT401, NT402: NetTie_2; NetTie-2_SMD_Pad2.0mm
NT601: GNDA; NetTie-2_SMD_Pad0.5mm
Q101, Q102, Q104: BSS138; SOT-23
Q103, Q301: IRLML2502; SOT-23
R101, R102: 1k; R_0603_1608Metric
R103, R104, R308, R502: 220; R_0603_1608Metric
R105, R106, R107, R108, R113, R114, R115, R301: 100; R_0603_1608Metric
R109, R110, R111, R112, R311: 100k; R_0603_1608Metric
R302, R304: 470k; R_1206_3216Metric
R303: 2.70k; R_0603_1608Metric
R307, R501: 10k; R_0603_1608Metric
R401, R402, R403: 120; R_0603_1608Metric
RL301: JW2; Relay_DPDT_Panasonic_JW2
SW201: RESET; SW_Push_1P1T_NO_CK_KMR2
TP101: ADC1_IN8; PinHeader_1x01_P1.27mm_Vertical
TP102: TIM3_CH2; PinHeader_1x01_P1.27mm_Vertical
TP201: PC4; PinHeader_1x01_P1.27mm_Vertical
TP202: PC15; PinHeader_1x01_P1.27mm_Vertical
U201: STM32G474RETx; LQFP-64_10x10mm_P0.5mm
U302: AMC3330; SOIC-16W_7.5x10.3mm_P1.27mm
U303, U501: MCA1101-50-5; SOIC-16W_7.5x10.3mm_P1.27mm
U401: ISO1500; SSOP-16_3.9x4.9mm_P0.635mm
U402, U403: ISO1050DUB; SOP-8_6.62x9.15mm_P2.54mm
U404: TMR_1-0511; Converter_DCDC_TRACO_TMR-1-xxxx_Single_THT
U601, U602: TPS7A0333PDBVR; SOT-23-5
Y201: 12 MHz; Crystal_SMD_SeikoEpson_TSX3225-4Pin_3.2x2.5mm

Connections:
+3V3: C201.1, C202.1, C203.1, C204.1, C206.1, C309.1, C310.1, C401.1, C402.1, C403.1, C604.1, D101.2 (A), D102.2 (A), J201.1, JP202.3 (B), R101.2, U201.1 (VBAT), U201.16 (VDD), U201.32 (VDD), U201.48 (VDD), U201.64 (VDD), U302.12 (VDD), U401.1 (VCC1), U402.1 (VCC1), U403.1 (VCC1), U602.5 (OUT)
+5V: C312.1, C501.1, C601.1, C602.1, J101.1, J108.1, J108.2, JP301.3 (B), NT401.1, NT403.1, R307.2, R501.2, U303.10 (VCC), U404.2 (+VIN), U501.10 (VCC), U601.1 (IN), U601.3 (EN), U602.1 (IN), U602.3 (EN)
+12V: J102.1, J109.2, J110.6, JP301.1 (A)
/AC grid/AMC3330_OUTN: U201.13 (PA1), U302.10 (OUTN)
/AC grid/AMC3330_OUTP: U201.12 (PA0), U302.11 (OUTP)
/AC grid/Contactor_{Grid}: R301.1, U201.30 (PB10)
/AC grid/Igrid_{+}: C313.1, R308.2, U201.9 (PC1)
/AC grid/L1_{grid_sw}: RL301.3, RL301.6, U303.5 (IP-), U303.6 (IP-), U303.7 (IP-), U303.8 (IP-)
/AC grid/L1_{grid}: J302.2, R304.2, RL301.4, RL301.5
/AC grid/L1_{inverter}: J302.3, U303.1 (IP+), U303.2 (IP+), U303.3 (IP+), U303.4 (IP+)
/AC grid/N: J302.1, R302.1
/AC grid/nFAULT_{MCA1101}: R307.1, U201.14 (PA2), U303.9 (~FAULTB)
/BMS_GND: J110.5, Q103.3 (D)
/Communication/5V_CAN1: C406.1, NT401.2, U403.8 (VCC2)
/Communication/5V_CAN2: C405.1, NT403.2, U402.8 (VCC2)
/Communication/5V_RS485: C404.1, C407.1, U401.10 (VCC2), U401.16 (VCC2), U404.4 (+VOUT)
/Communication/CAN1_{RX}: U201.45 (PA11), U403.2 (RXD)
/Communication/CAN1_{TX}: U201.62 (PB9), U403.3 (TXD)
/Communication/CAN2_{RX}: U201.58 (PB5), U402.2 (RXD)
/Communication/CAN2_{TX}: U201.59 (PB6), U402.3 (TXD)
/Communication/GND_CAN1: C406.2, NT402.2, U403.5 (GND2)
/Communication/GND_CAN2: C405.2, NT404.2, U402.5 (GND2)
/Communication/GND_RS485: C404.2, C407.2, D401.2 (A2), D403.1 (A1), U401.9 (GND2), U401.15 (GND2), U404.6 (-VOUT)
/Communication/RS485_{EN}: U201.57 (PB4), U401.4 (~RE), U401.5 (DE)
/Communication/RS485_{RX}: U201.55 (PD2), U401.3 (R)
/Communication/RS485_{TX}: U201.54 (PC12), U401.6 (D)
/Communication/UART_{RX}: J404.2, U201.53 (PC11)
/Communication/UART_{TX}: J404.1, U201.52 (PC10)
/Cont_{Bat2DCboost}: J110.1, R113.2
/DCcurrent_sense/CS+: J502.1, U501.1 (IP+), U501.2 (IP+), U501.3 (IP+), U501.4 (IP+)
/DCcurrent_sense/CS-: J502.2, U501.5 (IP-), U501.6 (IP-), U501.7 (IP-), U501.8 (IP-)
/DCcurrent_sense/Ipv_{+}: C502.1, R502.2, U201.23 (PC5)
/DCcurrent_sense/nFAULT_{MCA1101}: R501.1, U201.11 (PC3), U501.9 (~FAULTB)
/Microcontroller/+3V3A_{MCU}: C207.1, C208.1, C211.1, C603.1, U201.28 (VREF+), U201.29 (VDDA), U601.5 (OUT)
/Microcontroller/ADC1_IN8: TP101.1, U201.10 (PC2)
/Microcontroller/ADC2_IN3: J111.1, U201.20 (PA6)
/Microcontroller/ADC2_IN4: J111.2, U201.21 (PA7)
/Microcontroller/ADC2_IN12: J105.2, U201.26 (PB2)
/Microcontroller/BOOT0: JP202.2 (C), U201.61 (PB8)
/Microcontroller/EmergencyOFF: R102.2, U201.51 (PA15)
/Microcontroller/FB_Boost_{EN}: J106.9, U201.60 (PB7)
/Microcontroller/FB_Boost_{OverTemp}: J106.7, U201.46 (PA12)
/Microcontroller/FB_Boost_{PWMA}: J106.3, U201.34 (PB12), U201.44 (PA10)
/Microcontroller/FB_Boost_{PWMB}: J106.1, U201.35 (PB13), U201.37 (PB15)
/Microcontroller/FB_Boost_{VdcData}: J106.5, U201.56 (PB3)
/Microcontroller/FB_Grid_{EN}: J107.9, U201.36 (PB14)
/Microcontroller/FB_Grid_{OverTemp}: J107.7, U201.33 (PB11)
/Microcontroller/FB_Grid_{PWMA}: J107.3, U201.42 (PA8)
/Microcontroller/FB_Grid_{PWMB}: J107.1, U201.43 (PA9)
/Microcontroller/FB_Grid_{VdcData}: J107.5, U201.19 (PA5)
/Microcontroller/HRTIM1CH_{E1}: J104.2, U201.40 (PC8)
/Microcontroller/HRTIM1CH_{E2}: J104.1, U201.41 (PC9)
/Microcontroller/HRTIM1CH_{F1}: J104.4, U201.38 (PC6)
/Microcontroller/HRTIM1CH_{F2}: J104.3, U201.39 (PC7)
/Microcontroller/LED1: R103.1, U201.24 (PB0)
/Microcontroller/LED2: R104.1, U201.25 (PB1)
/Microcontroller/NRST: C205.1, SW201.1 (A), U201.7 (PG10)
/Microcontroller/PF0: C209.2, U201.5 (PF0), Y201.1
/Microcontroller/PF1: C210.2, U201.6 (PF1), Y201.3
/Microcontroller/SWCLK: J201.2, U201.50 (PA14)
/Microcontroller/SWDIO: J201.3, U201.49 (PA13)
/Microcontroller/TIM3_CH2: TP102.1, U201.18 (PA4)
Aux_OpenDrain: R106.1, U201.17 (PA3)
BMS_Power: R105.1, U201.8 (PC0)
CAN2_{H}: J110.4, R401.1, U402.7 (CANH)
CAN2_{L}: J110.3, R401.2, U402.6 (CANL)
Contactor_{Bat2DCboost}: R107.1, U201.2 (PC13)
Contactor_{Bat2Inverter}: R108.1, U201.3 (PC14)
GND: C201.2, C202.2, C203.2, C204.2, C205.2, C206.2, C209.1, C210.1, C309.2, C310.2, C311.2, C312.2, C313.2, C401.2, C402.2, C403.2, C501.2, C601.2, C602.2, C604.2, J101.2, J102.2, J106.2, J106.4, J106.6, J106.8, J106.10, J107.2, J107.4, J107.6, J107.8, J107.10, J201.4, J404.3, JP202.1 (A), NT402.1, NT404.1, NT601.2, Q101.2 (S), Q102.2 (S), Q103.2 (S), Q104.2 (S), Q301.2 (S), R109.1, R110.1, R111.1, R112.1, R311.1, SW201.2 (B), U201.15 (VSS), U201.31 (VSS), U201.47 (VSS), U201.63 (VSS), U302.9 (GND), U302.15 (DCDC_GND), U303.11 (GND), U303.14 (GND2), U303.15 (GND), U303.16 (VOC), U401.2 (GND1), U401.8 (GND1), U402.4 (GND1), U403.4 (GND1), U404.1 (-VIN), U501.11 (GND), U501.14 (GND2), U501.15 (GND), U501.16 (VOC), U601.2 (GND), U602.2 (GND), Y201.2, Y201.4
GNDA: C207.2, C208.2, C211.2, C502.2, C603.2, J105.1, NT601.1, U201.27 (VSSA)
unnamed: D101.1 (K), R103.2
unnamed: D102.1 (K), R104.2
unnamed: D301.2 (A), Q301.3 (D), RL301.8
unnamed: D301.1 (K), JP301.2 (C), RL301.1
unnamed: D401.1 (A1), D402.2 (A2), J402.1, R403.1, U401.12 (A)
unnamed: D402.1 (A1), D403.2 (A2), J402.2, R403.2, U401.13 (B)
unnamed: J103.1, R101.1
unnamed: J103.2, R102.1
unnamed: J109.1, R115.2
unnamed: J110.2, R114.2
unnamed: J401.1, R402.1, U403.6 (CANL)
unnamed: J401.2, R402.2, U403.7 (CANH)
unnamed: Q101.3 (D), R113.1
unnamed: Q101.1 (G), R107.2, R110.2
unnamed: Q102.3 (D), R114.1
unnamed: Q102.1 (G), R108.2, R112.2
unnamed: Q103.1 (G), R105.2, R111.2
unnamed: Q104.3 (D), R115.1
unnamed: Q104.1 (G), R106.2, R109.2
unnamed: Q301.1 (G), R301.2, R311.2
unnamed: TP201.1, U201.22 (PC4)
unnamed: TP202.1, U201.4 (PC15)
unnamed: C304.2, C305.2, C306.1, C307.2, C308.2, NT301.2, U302.2 (DCDC_HGND), U302.8 (HGND)
unnamed: C311.1, U302.13 (LDO_OUT), U302.16 (DCDC_IN)
unnamed: C304.1, C305.1, C306.2, U302.1 (DCDC_OUT), U302.3 (HLDO_IN)
unnamed: C307.1, C308.1, U302.5 (HLDO_OUT)
unnamed: C301.2, NT301.1, R303.2, R304.1, U302.7 (INN)
unnamed: C301.1, R302.2, R303.1, U302.6 (INP)
unnamed: R308.1, U303.12 (Vout)
unnamed: R502.1, U501.12 (Vout)

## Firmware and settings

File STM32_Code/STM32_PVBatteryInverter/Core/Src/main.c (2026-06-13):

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
/* Includes ------------------------------------------------------------------*/
#include "main.h"

/* USER CODE BEGIN Includes */
#include <stdlib.h>
#include <stdbool.h>
#include <stdio.h>

#include <string.h>

#include "common.h"
#include "monitoring.h"
#include "gpio.h"
#include "can_bus.h"
#include "ac_control.h"
#include "dc_control.h"
#include "sys_mode_controller.h"
#include "BatteryManagement/bms_types.h"
#include "electricity_meter.h"
#include "power_controller.h"
#include "battery.h"
#include <sml/sml_crc16.h>
#include <modbus_hybridinverter.h>


// todo
typedef struct {
    uint16_t cell_voltage_max_mV;
    uint16_t cell_voltage_max_index;
    uint16_t cell_voltage_min_mV;
    uint16_t cell_voltage_min_index;
} __attribute__((__packed__)) csc_cell_volt_min_max_t;

/* USER CODE END Includes */

/* USER CODE BEGIN PD */
#define uSend(x) uartSend((char *)x, sizeof x -1)
/* USER CODE END PD */

ADC_HandleTypeDef hadc1;
ADC_HandleTypeDef hadc2;
DMA_HandleTypeDef hdma_adc1;
DMA_HandleTypeDef hdma_adc2;

COMP_HandleTypeDef hcomp2;

FDCAN_HandleTypeDef hfdcan2;

HRTIM_HandleTypeDef hhrtim1;

IWDG_HandleTypeDef hiwdg;

LPTIM_HandleTypeDef hlptim1;

TIM_HandleTypeDef htim1;
TIM_HandleTypeDef htim2;
TIM_HandleTypeDef htim3;
TIM_HandleTypeDef htim4;

UART_HandleTypeDef huart5;
UART_HandleTypeDef huart3;
DMA_HandleTypeDef hdma_uart5_tx;
DMA_HandleTypeDef hdma_uart5_rx;
DMA_HandleTypeDef hdma_usart3_tx;

/* USER CODE BEGIN PV */
char tx_buf[64];
uint8_t tx_len;

UART_HandleTypeDef* huart_rs485;
UART_HandleTypeDef* huart_debug;
mbus_t modbus;

uint16_t ADC1ConvertedData[2];
uint16_t ADC2ConvertedData[1];
volatile uint16_t debug_sigma_delta_re;

volatile uint16_t id;
control_ref_t ctrl_ref;
volatile bool print_request;

volatile uint32_t cnt_1Hz;
volatile uint32_t cntErr_1Hz;

volatile uint16_t debug_v_dc_FBboost_sincfilt_100mV;
volatile uint16_t debug_v_dc_FBgrid_sincfilt_100mV;

extern volatile int16_t debug_v_ac_rms_100mV;
#if SENSOR_CALIBRATION_MODE == 1
extern volatile int16_t debug_v_ac_100mV;
extern volatile int16_t debug_i_ac_10mA;
volatile int16_t debug_i_dc_filt_10mA;
#endif //SENSOR_CALIBRATION_MODE

extern volatile int16_t debug_i_ac_ref_amp_10mA;


uint8_t ubKeyNumber = 0x0;

/* USER CODE END PV */

void SystemClock_Config(void);
static void MX_GPIO_Init(void);
static void MX_DMA_Init(void);
static void MX_ADC1_Init(void);
static void MX_ADC2_Init(void);
static void MX_FDCAN2_Init(void);
static void MX_HRTIM1_Init(void);
static void MX_TIM1_Init(void);
static void MX_TIM2_Init(void);
static void MX_TIM3_Init(void);
static void MX_TIM4_Init(void);
static void MX_UART5_Init(void);
static void MX_USART3_UART_Init(void);
static void MX_IWDG_Init(void);
static void MX_LPTIM1_Init(void);
static void MX_COMP2_Init(void);
/* USER CODE BEGIN PFP */
static void FDCAN_Config(void);

/* USER CODE END PFP */

/* USER CODE BEGIN 0 */


void uartSend(char* ptr, int len)
{
    HAL_UART_Transmit(huart_debug, (uint8_t *)ptr,len, 10);
}

void uSendInt(int value)
{
	itoa(value, tx_buf, 10);
	tx_len=strlen(tx_buf);
	HAL_UART_Transmit(huart_debug, (uint8_t *)tx_buf, tx_len, 10);
}

void uSend_1m(int int_value)
{
	float value = int_value/1000.0;
	tx_len = snprintf(NULL, 0, "%.03f", value);
	char *str = (char *)malloc(tx_len + 1);
	snprintf(str, tx_len + 1, "%f.03", value);
	HAL_UART_Transmit(huart_debug, (uint8_t *)str, tx_len, 10);
	free(str);
}

void uSend_10m(int int_value)
{
	float value = int_value/100.0;
	tx_len = snprintf(NULL, 0, "%.02f", value);
	char *str = (char *)malloc(tx_len + 1);
	snprintf(str, tx_len + 1, "%f.02", value);
	HAL_UART_Transmit(huart_debug, (uint8_t *)str, tx_len, 10);
	free(str);
}

void uSend_100m(int int_value)
{
	float value = int_value/10.0;
	tx_len = snprintf(NULL, 0, "%.01f", value);
	char *str = (char *)malloc(tx_len + 1);
	snprintf(str, tx_len + 1, "%f.01", value);
	HAL_UART_Transmit(huart_debug, (uint8_t *)str, tx_len, 10);
	free(str);
}


int mbus_send(const mbus_t context, const uint8_t* data, const uint16_t size)
{
	// V1: blocking during send
	//HAL_Delay(1);
	if (HAL_UART_Transmit( huart_rs485, (uint8_t*) data, size, 1000) == HAL_OK) {
		return size;
	}

	// V2: use DMA
//	if (HAL_UART_Transmit_DMA( huart_rs485, (uint8_t*) data, size) == HAL_OK) {
//		return size;
//	}

	return 0;
}


void resetWatchdog()
{
	// Watchdog runs at 32/8=4kHz -> ~1sec for 4095
    /* Refresh IWDG: reload counter */
    if(HAL_IWDG_Refresh(&hiwdg) != HAL_OK) {
      /* Refresh Error */
      Error_Handler();
    }
}


void HAL_LPTIM_AutoReloadMatchCallback(LPTIM_HandleTypeDef *hlptim)
{
	cnt_1Hz++;
	if (get_sys_errorcode() != EC_NO_ERROR) {
		cntErr_1Hz++;
	}
}


void fill_monitor_vars_sys(monitor_vars_t* mon_vars)
{
	mon_vars->id = id;
	mon_vars->sys_mode = get_sys_mode();
	mon_vars->sys_errcode = get_sys_errorcode();

	fill_monitor_vars_dc(mon_vars);
	fill_monitor_vars_ac(mon_vars);

	mon_vars->ctrl_mode_AC = ctrl_ref.mode;
	mon_vars->p_ac_ref = ctrl_ref.p_ac_rms;

#if SYSTEM_HAS_BATTERY == 1
	const batteryStatus_t* battery = get_batteryStatus();
	mon_vars->bat_p = battery->power_W;
	mon_vars->soc_10mPercent = battery->soc_percent*100;
#endif //SYSTEM_HAS_BATTERY
}


#if COMM_READ_ELECTRICITY_METER == 1
// sends monitor_vars + header + crc via RS485
static void send_inverterdata()
{
	// if BMS is not part of the bus, add: Struct BMS Data : onoff Soc V I vmin vmax

	static monitor_packet_t mon_packet = {.header=0xDEADBEEF, 0};  // static for DMA
	fill_monitor_vars_sys(&mon_packet.monitor_vars);

	mon_packet.crc = sml_crc16_calculate((uint8_t *)&mon_packet.monitor_vars, sizeof(mon_packet.monitor_vars));

	if (HAL_UART_Transmit(huart_rs485, (uint8_t *)&mon_packet, sizeof(mon_packet), 10) != HAL_OK) {
		Error_Handler();
	}
//	if (HAL_UART_Transmit_DMA(huart_rs485, (uint8_t *)&mon_vars_snapshot, sizeof(mon_vars_snapshot)) != HAL_OK) {
//		Error_Handler();
//	}
}
#endif


void reinitUART(UART_HandleTypeDef *huart, uint32_t BaudRate)
{
	if (huart->Init.BaudRate != BaudRate) {
		huart->Init.BaudRate = BaudRate;
		if (HAL_UARTEx_DisableFifoMode(huart) != HAL_OK) {
			Error_Handler();
		}
		if (HAL_UART_Init(huart) != HAL_OK) {
			Error_Handler();
		}
		if (HAL_UARTEx_EnableFifoMode(huart) != HAL_OK) {
			Error_Handler();
		}
	}
}


void shutdownAll()
{
	gatedriverAC(0);
	gatedriverDC(0);
	contactorAC(0);
	contactorBattery(0);
#if SYSTEM_HAS_BATTERY == 1
	battery_state_request(CMD_BAT_OFF);  // todo: check CMD_BMS_OFF__BAT_OFF
#endif //SYSTEM_HAS_BATTERY
}

int el_meter_status;

void calc_and_wait(uint32_t delay)
{
	resetWatchdog();
	calc_async_dc_control();

#if COMM_READ_ELECTRICITY_METER == 0
	for (uint32_t i=0; i<delay; i++) {
		calc_async_dc_control();
		if (!monitoring_binary_en) {
			HAL_Delay(1);  //ms
		}
	}
#endif


#if COMM_READ_ELECTRICITY_METER == 1
	if (!monitoring_binary_en) {  // smart meter polling read takes too much time
		reinitUART(huart_rs485, 9600);
		resetWatchdog();
#define DUMMY_METER 0
#if DUMMY_METER == 1
		int el_meter_status = EL_METER_OKAY;
#else
		el_meter_status = electricity_meter_read(huart_rs485);
#endif //DUMMY_METER
		//HAL_UART_Abort_IT(&huart1);
		if ( el_meter_status == EL_METER_OKAY) {
			ctrl_ref.p_pcc_prev = ctrl_ref.p_pcc;
#if DUMMY_METER == 1
			const batteryStatus_t* battery = get_batteryStatus();
			//ctrl_ref.p_pcc = 50+battery->power_W;  // p_bat negative is discharging AC 4sec on 4sec off
			//ctrl_ref.p_pcc = 500;  // simulate load
			ctrl_ref.p_pcc = -100;  // simulate PV feedin
#else
			ctrl_ref.p_pcc = electricity_meter_get_power();
#endif //DUMMY_METER
#if SYSTEM_HAS_BATTERY == 1
			ctrl_ref.p_ac_pccCtrl = power_controller_step(modbus_reg_rw.p_pcc_ref_W, ctrl_ref.p_pcc, get_p_ac_max());
#endif //SYSTEM_HAS_BATTERY
		} else if (el_meter_status == EL_METER_CONN_ERR ) {
			ctrl_ref.p_ac_pccCtrl = 0;
		}

		if (el_meter_status == EL_METER_OKAY || el_meter_status == EL_METER_CONN_ERR ) {
			reinitUART(huart_rs485, 115200);
			calc_async_dc_control();

			if (async_battery_communication()) {
				send_inverterdata();

				// receive commands from external energy management system
//#define RX_MAX_CMD_LEN (sizeof("p_bat_chg_max65535\n")+5)
#define RX_MAX_CMD_LEN (sizeof(modbus_reg_rw_t)+8)
				uint8_t rx_buf[RX_MAX_CMD_LEN];

				for (uint16_t i = 0; i < 10; i++) {
					uint16_t rx_len = 0;
					HAL_UARTEx_ReceiveToIdle(huart_rs485, rx_buf, RX_MAX_CMD_LEN, &rx_len, 10);  // 10 x 10ms rx window

					for (uint16_t j = 0; j < rx_len; j++) {
						mbus_poll(modbus, rx_buf[j]);
					}
				}
				apply_sys_mode_cmd(&ctrl_ref);
				mbus_flush(modbus);  // reset incomplete messages
			}
		}
	} else {
		reinitUART(huart_rs485, 115200);
		resetWatchdog();
		calc_async_dc_control();
		async_battery_communication();
	}
#endif //COMM_READ_ELECTRICITY_METER

	calc_p_ac(&ctrl_ref);

	resetWatchdog();
	async_monitor_check(huart_debug);
}


// +-50A sensor range with 3.3V ADC:
// −62.1A to +32.1A
// analog watchdog: (dont use filtering in AWD1 because it does not work with sequence mode (scan conversion))
// oversampling is enabled (8xOSR; 3bit shift -> 4-(log2(8)/3 -1) = 4bit shift down
#define I_AC_AWD_THRESHOLD_HIGH ((E_I_AC_PULSE_MAX_AMP_10mA/IAC_RAW_TO_10mA + IAC_OFFSET_RAW)/16)
#define I_AC_AWD_THRESHOLD_LOW ((-E_I_AC_PULSE_MAX_AMP_10mA/IAC_RAW_TO_10mA + IAC_OFFSET_RAW)/16)
// for test
//#define I_AC_AWD_THRESHOLD_HIGH 208  // +16.0Ampere -> 1600/IAC_RAW_TO_10mA + 2632 = 3327 /16
//#define I_AC_AWD_THRESHOLD_LOW 121  // -16.0Ampere -> -1600/IAC_RAW_TO_10mA + 2632 = 1937 /16
//#define I_AC_AWD_THRESHOLD_HIGH 167  // +1.0Ampere -> 100/IAC_RAW_TO_10mA + 2632 = 2675 /16
//#define I_AC_AWD_THRESHOLD_LOW 162  // -1.0Ampere -> -100/IAC_RAW_TO_10mA + 2632 = 2589 /16
void HAL_ADC_LevelOutOfWindowCallback(ADC_HandleTypeDef* hadc)
{
	shutdownAll();
	set_sys_errorcode(EC_I_AC_PULSE_MAX);
}


void configure_analog_watchdog()
{
	/* Set ADC analog watchdog channels to be monitored */
	LL_ADC_SetAnalogWDMonitChannels(ADC1, LL_ADC_AWD1, LL_ADC_AWD_CHANNEL_7_REG);

	/* Set ADC analog watchdog thresholds */
	LL_ADC_ConfigAnalogWDThresholds(ADC1, LL_ADC_AWD1, I_AC_AWD_THRESHOLD_HIGH, I_AC_AWD_THRESHOLD_LOW);

	/*## Configuration of ADC interruptions ####################################*/
	// ADC1_2 interrupts are enabled in GUI
	/* Enable ADC analog watchdog 1 interruption */
	LL_ADC_EnableIT_AWD1(ADC1);
	LL_ADC_ClearFlag_AWD1(ADC1);
}


void HAL_ADC_ConvCpltCallback(ADC_HandleTypeDef *hadc)
{
	uint32_t start_ISR_cycles = DWT->CYCCNT;
	//static volatile uint16_t vdc_sinc_mix_100mV;
	static volatile uint16_t cnt20kHz_20ms = 0;

	/********************************************************/
	/* Highest priority: Grid control						*/
	/* 	execution rate: 20kHz								*/
	/* 	runtime: max18.4us									*/
	/*  max possible runtime without compare unit 3 change: */
	/*  25-5.1=19.9us										*/
	/********************************************************/

	// ADC1: two channels, Vac and i_ac
	// HRTIM1 triggers ADC once per period and DMA calls this callback if ADC1ConvertedData[2] is full
	// Thus, both channels in ADC1ConvertedData are updated in every call.
	if (hadc == &hadc1) {
		DEBUG_ISR GPIOC->BSRR = (1<<4);  // set Testpin TP201 PC4  T1
		// With 4xOversampling: 4.3us-0.44us=3.9us after mid of PWM period (see documentation/img folder)
		// With 8xOversampling: 7.0us-0.44us=6.6us after mid of PWM period -> 25-6.6=18.4us for calculation

		// start ADC2 conversion, because ADC1 conversions are complete here and can't be disturbed by ADC2
		LL_ADC_REG_StartConversion(hadc2.Instance);

//		if (fast_mon_vars_trig) {
//			if (frame_nr < FAST_MON_FRAMES) {
//				fast_monitor_vars[frame_nr].v_ac_100mV = ADC1ConvertedData[0];
//				fast_monitor_vars[frame_nr].i_ac_10mA = ADC1ConvertedData[1];
//				fast_monitor_vars[frame_nr].i_ac_ref_amp_10mA = ADC2ConvertedData[0]/16;
//				frame_nr++;
//			}
//		}

		measVdcFBgrid();  // if runtime becomes critical, run this line after ac dutycycle calculation
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
int main(void)
{

  /* MCU Configuration--------------------------------------------------------*/

  /* Reset of all peripherals, Initializes the Flash interface and the Systick. */
  HAL_Init();

  /* Configure the system clock */
  SystemClock_Config();

  /* Initialize all configured peripherals */
  MX_GPIO_Init();
  MX_DMA_Init();
  MX_ADC1_Init();
  MX_ADC2_Init();
  MX_FDCAN2_Init();
  MX_HRTIM1_Init();
  MX_TIM1_Init();
  MX_TIM2_Init();
  MX_TIM3_Init();
  MX_TIM4_Init();
  MX_UART5_Init();
  MX_USART3_UART_Init();
  MX_IWDG_Init();
  MX_LPTIM1_Init();
  MX_COMP2_Init();
  /* USER CODE BEGIN 2 */

  /* Configure the overcurrent watchdog */
  configure_analog_watchdog();

  /* Configure the cycle counter for ISR runtime check */
  CoreDebug->DEMCR |= CoreDebug_DEMCR_TRCENA_Msk; // Enable Trace and debug blocks
  DWT->CTRL |= DWT_CTRL_CYCCNTENA_Msk;          // Enable CYCCNT register

  // Test battery contactor
#if TEST_BATTERY_CONTACTOR_MODE == 1
  bmsPower(1);
  contactorBattery(1);
  set_sys_errorcode(EC_TEST_COMPLETE);  // prevent system operation
  while (1) {
	resetWatchdog();
  }
#endif

  /* Configure the FDCAN peripheral */
  FDCAN_Config();  // CAN2 is connected to Battery Cell Stack Controller CAN Bus

  /* Modbus interface */
  uint8_t modbus_tx_buf[STMODBUS_MAX_RESPONSE_SIZE] = {0};
  uint8_t modbus_rx_buf[STMODBUS_MAX_RESPONSE_SIZE] = {0};

  Modbus_Conf_t mb_config;
  mb_config.send = &mbus_send;
  mb_config.sendbuf = modbus_tx_buf;
  mb_config.sendbuf_sz = STMODBUS_MAX_RESPONSE_SIZE;
  mb_config.recvbuf = modbus_rx_buf;
  mb_config.recvbuf_sz = STMODBUS_MAX_RESPONSE_SIZE;
  modbus = mbus_hybridinverter_open(&mb_config);

// Set to 1 to swap UARTs for Modbus debugging without using RS485 transceivers
#if 0
  huart_rs485 = &huart3;
  huart_debug = &huart5;
#else  // production
  huart_rs485 = &huart5;  // binary communication
  huart_debug = &huart3;  // text messages
#endif

  // DCDC sw-freq: 20kHz 170MHz/20kHz = 8500 -> Period = 4249
  // DCDC ctrl-freq: 100Hz -> Repetition Counter = 200
  // Todo check ADC clock

  // ###########################
  // ### Timer configuration ###
  // ###########################

  // start PWM for PV boost Half-bridge 1 (PWMA)
  if (   HAL_TIM_PWM_Start(&htim1, TIM_CHANNEL_3) != HAL_OK) {
    /* PWM Generation Error */
    Error_Handler();
  }
  // start PWM for PV boost Half-bridge 2 (PWMB)
  if (  HAL_TIMEx_PWMN_Start(&htim1, TIM_CHANNEL_1) != HAL_OK) {
    /* PWM Generation Error */
    Error_Handler();
  }
  // start PWM timer for PV boost Full-bridge
  if (  HAL_TIM_Base_Start_IT(&htim1) != HAL_OK)
  {
    Error_Handler();
  }

  // start timer for 1Hz system timebase
  #define LPTIM_TICKS_PER_SEC (32000/128)  // timer has 32kHz oscillator and DIV128 -> 250Hz
  if (HAL_LPTIM_Counter_Start_IT(&hlptim1, LPTIM_TICKS_PER_SEC) != HAL_OK) {
    Error_Handler();
  }

  // start Sigma-delta-ADC counter for Vdc FB_boost
  HAL_TIM_Base_Start(&htim4);

  // start Sigma-delta-ADC counter for Vdc FB_grid
  HAL_TIM_Base_Start(&htim2);

  // start PWM timer for grid Full-bridge
  if (   HAL_HRTIM_WaveformOutputStart(&hhrtim1, HRTIM_OUTPUT_TA1+HRTIM_OUTPUT_TA2) != HAL_OK)
  {
    /* PWM Generation Error */
    Error_Handler();
  }

  // Shift ADC trigger for phase correct ADC sampling
  // ADC oversample 8x need to be shifted 4x (15/42.5MHz) = 1.41176us
  // one up-down PWM period counts 2x8500 in 50us
  // 1.41176us/50us * (2*8500) = 480
  // 8500-480=8020  // Set this value in GUI compare unit 3, then ISR starts execution 5.1us after CNT_MAX (period)
  // Without the extra compare unit (using period of TimerA for ADC trigger) is takes 6.6us until DMA triggers the HAL_ADC_ConvCpltCallback

  if (   HAL_HRTIM_WaveformCounterStart(&hhrtim1, HRTIM_TIMERID_TIMER_A) != HAL_OK)
  {
    /* PWM Generation Error */
    Error_Handler();
  }


  // #########################
  // ### DMA configuration ###
  // #########################
  if ( HAL_ADC_Start_DMA(&hadc1, (uint32_t *)ADC1ConvertedData, sizeof(ADC1ConvertedData)/sizeof(ADC1ConvertedData[0]))  != HAL_OK)
  {
    Error_Handler();
  }

  if ( HAL_ADC_Start_DMA(&hadc2, (uint32_t *)ADC2ConvertedData, sizeof(ADC2ConvertedData)/sizeof(ADC2ConvertedData[0]))  != HAL_OK)
  {
    Error_Handler();
  }

  //__HAL_TIM_SetCompare(&htim1, TIM_CHANNEL_3, 2125);  //update pwm value 50% dutycycle

  /* Start COMP2 for 5V undervoltage protection */
  // test with load resistor:
  // 15.6Ohm: 4.67 to 4.69V does not trigger
  // 13.3Ohm: 4.60 to 4.65V triggers comparator
  // 10Ohm: slow 20ms drop to 3.86V triggers comparator and caused sigmadelta sensor error when comparator was not active.
  if(HAL_COMP_Start(&hcomp2) != HAL_OK) {
    Error_Handler();
  }

  uSend("PVBattery Inverter  ");
  uSend(__DATE__ " ");
  uSend(__TIME__);
  uSend("\n");
  GPIOB->BSRR = (1<<0);  // disable red LED

#define I_AC_AWD_THRESHOLD_to_10mA(x) ((x*16-IAC_OFFSET_RAW)*IAC_RAW_TO_10mA)
  uSend("I_AC analog watchdog config:\n");
  uSend(" high: ");
  uSendInt(I_AC_AWD_THRESHOLD_HIGH);
  uSend(" = ");
  uSend_10m(I_AC_AWD_THRESHOLD_to_10mA(I_AC_AWD_THRESHOLD_HIGH));
  uSend(" A\n");
  uSend(" low:  ");
  uSendInt(I_AC_AWD_THRESHOLD_LOW);
  uSend(" = ");
  uSend_10m(I_AC_AWD_THRESHOLD_to_10mA(I_AC_AWD_THRESHOLD_LOW));
  uSend(" A\n\n");

  /*## Check if the system has resumed from IWDG reset ####################*/
  HAL_PWR_EnableBkUpAccess();  // for access to flags written by the bootloader

  //  if (__HAL_RCC_GET_FLAG(RCC_FLAG_IWDGRST) != 0x00u) {  // Does not work, because bootloader clears the flag
  if (TAMP->BKP0R == 0x57444721) {  // "WDG!"
    TAMP->BKP0R = 0;

    uSend("Watchdog caused reset!");
    uSend("\n");
    set_sys_errorcode(EC_WATCHDOG_RESET);  // prevent ongoing inverter turnon in case of software bug
    HAL_Delay(300);  //ms
  }
  /* Clear reset flags anyway */
  __HAL_RCC_CLEAR_RESET_FLAGS();

  bool uart_output_text = false;
  bool uart_input_text = true;

#if SENSOR_CALIBRATION_MODE == 1
  uart_output_text = true;
#endif //SENSOR_CALIBRATION_MODE

  /* USER CODE END 2 */

  /* Infinite loop */
  /* USER CODE BEGIN WHILE */
  while (1)
  {
    /* USER CODE END WHILE */

    /* USER CODE BEGIN 3 */

	checkErrors();
	if (get_sys_mode() != OFF) GPIOB->BRR = (1<<1);  // enable green LED
	calc_and_wait(250);  //ms
	calc_and_wait(250);  //ms
	GPIOB->BSRR = (1<<1);  // disable green LED
	calc_and_wait(250);  //ms

	sys_mode_ctrl_step(&ctrl_ref);


	// UART
	if (print_request && uart_output_text) {
		print_request = false;

		calc_and_wait(250);  //ms

#if 0  // debug print battery info
		/************************/
		/* print battery status */
		/************************/

#if SYSTEM_HAS_BATTERY == 1
		const batteryStatus_t* battery = get_batteryStatus();
#endif //SYSTEM_HAS_BATTERY

		uSend("\nBatteryStatus\n");

		for (int c=0; c<(4*14); c++) {

			uSend("Temp");
			if (c<=8)
				uSend(" ");
			uSendInt(c+1);
			uSend(" ");
			uSendInt(get_battery_temperature(c));
			uSend("\n");
		}

		uint8_t nr_cells_balancing = 0;

		if (battery->voltage_100mV != 0) {
			for (int c=0; c<96; c++) {
				if (c%12 == 0) uSend(" ");
				uSend("Vc");
				if (c<=8)
					uSend(" ");
				uSendInt(c+1);
				uSend(" ");
				uSend_1m(get_battery_vCell_mV(c));

				if (get_battery_balancingState(c)) {
					uSend(" balancing");
					nr_cells_balancing++;
				}
				uSend("\n");
			}
		}
		uSend("nr_cells_balancing ");
		uSendInt(nr_cells_balancing);
		uSend("\n");

		int16_t vCellDIFF_mV = battery->maxVcell_mV - battery->minVcell_mV;
		uSend("vCellDIFF_mV ");
		uSend_1m(vCellDIFF_mV);
		uSend("\n");

		for (int csc=0; csc<4;csc++) {
			if (get_battery_csc_err(csc)) {
				uSend("Err in CSC");
				uSendInt(csc+1);
				uSend("\n");
				for (uint8_t bit=0; bit<64; bit++) {
					if ( (1<<bit) & get_battery_csc_err(csc)) {
						const char* strerr = get_battery_csc_err_str(bit);
						tx_len=strlen(strerr);
						HAL_UART_Transmit(huart_debug, (uint8_t *)strerr, tx_len, 10);
						uSend("\n");
					}
				}
			}
		}
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

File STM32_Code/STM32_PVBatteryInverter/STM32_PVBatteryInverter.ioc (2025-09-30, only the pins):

Mcu.UserName=STM32G474RETx
PA0.Signal=ADC1_IN1
PA1.Signal=ADC1_IN2
PA10.Signal=S_TIM1_CH3
PA11.Signal=FDCAN1_RX
PA12.Signal=GPXTI12
PA13.Signal=SYS_JTMS-SWDIO
PA14.Signal=SYS_JTCK-SWCLK
PA15.Signal=GPIO_Input
PA2.Signal=GPXTI2
PA3.Signal=GPIO_Output
PA4.Signal=S_TIM3_CH2
PA5.Signal=S_TIM2_ETR
PA6.Signal=ADC2_IN3
PA7.Signal=COMP2_INP
PA8.Signal=HRTIM1_CHA1
PA9.Signal=HRTIM1_CHA2
PB0.Signal=GPIO_Output
PB1.Signal=GPIO_Output
PB10.Signal=GPIO_Output
PB11.Signal=GPXTI11
PB13.Signal=TIM1_CH1N
PB14.Signal=GPIO_Output
PB15.Signal=TIM1_CH3N
PB2.Signal=ADC2_IN12
PB3.Signal=S_TIM4_ETR
PB4.Signal=UART5_DE
PB5.Signal=FDCAN2_RX
PB6.Signal=FDCAN2_TX
PB7.Signal=GPIO_Output
PB9.Signal=FDCAN1_TX
PC0.Signal=GPIO_Output
PC1.Signal=ADC1_IN7
PC10.Signal=USART3_TX
PC11.Signal=USART3_RX
PC12.Signal=UART5_TX
PC13.Signal=GPIO_Output
PC14-OSC32_IN.Signal=GPIO_Output
PC15-OSC32_OUT.Signal=GPIO_Output
PC3.Signal=GPXTI3
PC4.Signal=GPIO_Output
PC5.Signal=ADC2_IN11
PC6.Signal=HRTIM1_CHF1
PC7.Signal=HRTIM1_CHF2
PC8.Signal=HRTIM1_CHE1
PC9.Signal=HRTIM1_CHE2
PD2.Signal=UART5_RX
PF0-OSC_IN.Signal=RCC_OSC_IN
PF1-OSC_OUT.Signal=RCC_OSC_OUT

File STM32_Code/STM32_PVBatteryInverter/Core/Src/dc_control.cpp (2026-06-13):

#include "stm32g4xx_hal.h"

#include <string.h>
#include <stdio.h>
#include <stdbool.h>
#include <algorithm>
#include <climits>


#include "common.h"
#include "config_pv.h"
#include "monitoring.h"
#include "gpio.h"
#include "dc_control.h"
#include "ac_control.h"
#include "battery.h"
#include "mpptracker.hpp"
#include "PICtrl.hpp"
#include "sys_mode_controller.h"

#include "BatteryManagement/STW_mBMS.hpp"
extern STW_mBMS bms;


// single PWM step has 1/170MHz = 5.88ns -> center aligned PWM -> 11.8ns
// deadtime is configured to 64ns (10k resistor)
#define MIN_PULSE 9  // min pulse duration is 106ns - 64ns deadtime = 42ns

volatile bool sys_mode_needs_battery = false;
extern volatile uint16_t v_dc_ref_100mV;

volatile uint16_t debug_dutyHS;

volatile uint16_t v_dc_FBboost_sincfilt_100mV;
volatile uint16_t v_dc_FBboost_filt50Hz_100mV;

volatile float p_dc_filt50Hz;  // power from DC boost stage
volatile float p_pv_filt1Hz;
volatile float v_pv_filt50Hz;
volatile float v_dc_filt50Hz;
volatile float i_pv_filt50Hz;
volatile bool mppt_calc_request;
volatile bool mppt_calc_complete;
volatile bool bat_protect_calc_request;

MPPTracker mppTracker(PVMODULE, MPPTPARAM, GMPPTPARAM);

volatile enum stateDC_t stateDC = INIT_DC;

#if ((NUM_MPPT_HALFBRIDGES == 1) && (MPPT_HALFBRIDGE_NR == 2))
	constexpr enum dcdc_mode_t DEFAULT_DCDC_MODE = DCDC_HB2;
#else
	constexpr enum dcdc_mode_t DEFAULT_DCDC_MODE = DCDC_HB1;
#endif

volatile enum dcdc_mode_t dcdc_mode = DEFAULT_DCDC_MODE;

static volatile uint32_t cnt_rel = 0;

static uint16_t p_ac_bat_chg_reduction = 0;  // if PV power is to high for battery, feed into AC grid

uint16_t get_p_ac_bat_chg_reduction()
{
	return p_ac_bat_chg_reduction;
}

uint16_t get_p_ac_max_dc_lim()
{
	float p_pv = p_dc_filt50Hz;
	if (p_pv < 0.0) p_pv = 0.0;  // prevent noise of current sensor
	return (get_p_bat_dischg_max() + p_pv);
}


uint16_t get_v_dc_FBboost_sincfilt_100mV()
{
	return v_dc_FBboost_sincfilt_100mV;
}


uint16_t get_v_dc_FBboost_filt50Hz_100mV()
{
	return v_dc_FBboost_filt50Hz_100mV;
}


float get_p_pv_filt1Hz()
{
	return p_pv_filt1Hz;
}


float get_p_dc_filt50Hz()
{
	return p_dc_filt50Hz;
}


float get_v_dc_filt50Hz()
{
	return v_dc_filt50Hz;
}


void fill_monitor_vars_dc(monitor_vars_t* mon_vars)
{
	mon_vars->stateDC = stateDC;
	mon_vars->dcdc_mode = dcdc_mode;
	mon_vars->dutyDC_HS = debug_dutyHS;
	mon_vars->p_dc_filt50Hz = p_dc_filt50Hz;
	mon_vars->v_dc_filt50Hz = v_dc_filt50Hz;

	mon_vars->v_dc_FBboost_sincfilt_100mV = v_dc_FBboost_sincfilt_100mV;
}


void calc_async_dc_control()
{
	if (mppt_calc_request) {
		// The measurement values of the first 50Hz cycle are not used because:
		// 1. The energy in the PV input capacitor has to be compensated, due to duty cycle change
		// 2. The delay of the analog filter for current measurement has to be taken into account
		// 3. Enough filtering/averaging for decent precision is already available
		// 4. The second measurement represents the current situation

		static float v_dc_filt50Hz_prev = v_dc_filt50Hz;
		// Because the current measurement is at the output of the DC link capacitors of the boost stage,
		// the voltage change in the DC link has to be taken into account.
		// C=2x560uF  U=361V  U_prev=360V
		// dE=0.5*C* (U^2 - U_prev^2)=0.404 Joule
		// f = 25Hz  -> p_cap_comp = f*dE = 10.1 Watt
		float p_cap_comp = MPPTPARAM.mppt_freq * 0.5 * 2*560e-6 * (v_dc_filt50Hz*v_dc_filt50Hz - v_dc_filt50Hz_prev*v_dc_filt50Hz_prev);
		mppTracker.step(p_dc_filt50Hz+p_cap_comp, v_pv_filt50Hz);
		v_dc_filt50Hz_prev = v_dc_filt50Hz;
		mppt_calc_request = false;
		mppt_calc_complete = true;
	}

	if (bat_protect_calc_request) {

		bat_protect_calc_request = false;

		constexpr float TC = 1.0f / DC_CTRL_FREQ_SLOW;  // 20ms execution interval

		static uint16_t cnt50Hz_1s = 0;
		static int32_t p_pv_sum;
		p_pv_sum += p_dc_filt50Hz;  // capacitor compensation can be neglected
		cnt50Hz_1s++;

		if (cnt50Hz_1s == DC_CTRL_FREQ_SLOW) {
			p_pv_filt1Hz = p_pv_sum/DC_CTRL_FREQ_SLOW;
			p_pv_sum = 0;
			cnt50Hz_1s = 0;
		}

		/**********************************************/
		/* Battery power limit -> AC power controller */
		/**********************************************/
		constexpr float T_Pbat_sensor_delay = 0.02;  // 20ms battery power estimation meas delay modelled as PT1-delay
		constexpr float T_sigma_Pbat = T_Pbat_sensor_delay + TC;

		// magnitude optimum method (Betragsoptimum) // ToDo: check if valid
		constexpr float kp_Pbat = 0.5;  // no gain in plant -> 0.5
		constexpr float ki_Pbat = 0.5 * 1/T_sigma_Pbat;
		static PICtrl piCtrl_Pac_Pbat(TC, kp_Pbat, ki_Pbat);

		int p_bat_50Hz = p_dc_filt50Hz - get_p_ac_filt50Hz();

//		uint16_t p_limit;

//		if (bms.batteryStatus.power_W > 0) {
//			p_limit = bms.p_charge_max();
//		} else {
//			p_limit = bms.p_discharge_max();
//		}

		uint16_t p_bat_chg_soft_max = get_p_bat_chg_soft_max();
		piCtrl_Pac_Pbat.step( (p_bat_50Hz - p_bat_chg_soft_max), 0, P_AC_MAX);

#if 0  // use if linear Vcell power limit in BMS code causes ringing
	    /**********************************************/
	    /* Battery Vcell limit -> AC power controller */
	    /**********************************************/
	    constexpr float T_Vcell_sensor_delay = 1.0;  // 1.0 sec battery cell voltage meas delay modelled as PT1-delay
	    constexpr float T_sigma_Vcell = T_Vcell_sensor_delay + TC;

	    // magnitude optimum method (Betragsoptimum) // ToDo: check if valid
	    constexpr float kp_Vcell = 0.5;  // no gain in plant -> 0.5
	    constexpr float ki_Vcell = 0.5 * 1/T_sigma_Vcell;
	    static PICtrl piCtrl_Pac_Vcell(TC, kp_Vcell, ki_Vcell);

	    // to reduce cell voltage by 1mV, Pbat has to be reduced Vbat*Ibat=Vbat*(Vcell/Rcell)
	    // e.g. 360Vbat 8mOhmCell 1mV reduction -> 360V*(1mV/8mOhm) = 45W
	    constexpr float PBAT_REDUCE_PER_MV = ((float)V_BAT_NOM) / bms.R_CELL_mOHM();

	    const batteryStatus_t* battery = get_batteryStatus();
		piCtrl_Pac_Vcell.step( PBAT_REDUCE_PER_MV*(battery->maxVcell_mV - bms.V_CELL_MAX_POWER_REDUCE_mV()), 0, P_AC_MAX);
#endif

		p_ac_bat_chg_reduction = piCtrl_Pac_Pbat.y;

		// Limit MPP Tracker
		float p_pv_max = battery_full() ? P_AC_MAX : (P_AC_MAX+get_p_bat_chg_hard_max());
		mppTracker.set_limit(MPPTPARAM.i_in_max, p_pv_max);
	}
}


void shutdownDC()
{
	gatedriverDC(0);
	contactorBattery(0);
}
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

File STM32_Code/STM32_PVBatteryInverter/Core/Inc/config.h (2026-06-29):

#ifndef INC_CONFIG_H
#define INC_CONFIG_H

#define SYS_MODE HYBRID_PCC_SENSOR
//#define SYS_MODE PV2AC
//#define SYS_MODE PV2BAT

#define COMM_READ_ELECTRICITY_METER 1  // listen for smart meter data and send inverterdata after reception
#define SYSTEM_HAS_BATTERY 1

#define USE_TRAFO_33V 0  // 0: high voltage grid. 1: test with 33V trafo (~30.5V with 9 extra windings for 15 cell LFP battery)

//ISR runtime measurement using testpin TP202(PC15) and TP201(PC4)
#define DEBUG_ISR if(0)  // 0: no pin toggling  1: enable pin toggling. Increases runtime and maybe ADC noise.

#define TEST_BATTERY_CONTACTOR_MODE 0
#define SENSOR_CALIBRATION_MODE 0  // 0: normal operation  1: UART output for sensor calibration; AC relay is disabled
#define PWM_TEST_MODE 0
// 0: normal operation
// 1: 50% dutycycle for all fullbridge outputs; AC relay is disabled
// 2: 90% HS dutycycle for boost converter, two periods only; AC relay is disabled

#ifndef SENSOR_CALIBRATION_MODE
#error "SENSOR_CALIBRATION_MODE has to be defined as 0 or 1"
#endif

#ifndef PWM_TEST_MODE
#error "PWM_TEST_MODE has to be defined as 0, 1 or 2"
#endif

#define VDC_MAX_MPPT_100mV 390*10        // 400V / 96cells = 4.167V
#define E_VDC_MAX_FB_BOOST_100mV 400*10  // worst case for battery if BMS fails: 408V / 96cells = 4.25V
#define E_VDC_MAX_FB_GRID_100mV 400*10   // worst case for battery if BMS fails: 408V / 96cells = 4.25V

/***********/
/* AC grid */
/***********/
#ifndef USE_TRAFO_33V
#error "USE_TRAFO_33V has to be defined as 0 or 1"
#endif

#if USE_TRAFO_33V == 1
#define VGRID_TRATIO 7  // transformer winding ratio
#elif USE_TRAFO_33V == 0
#define VGRID_TRATIO 1  // no transformer
#endif

#define VGRID_AMP 325/VGRID_TRATIO

//VDE 4105:
// 47.5 Hz to 49.0 Hz  ≥30 min
// 49.0 Hz to 51.0 Hz  unlimited
// 51.0 Hz to 51.5 Hz  ≥30 min
#define F_MIN 48
#define F_MAX 51

#define E_I_AC_RMS_MAX_CNT 15  // 15 samples @ 20kHz -> 750µs
#define E_I_AC_RMS_MAX_AMP_10mA (17.2 * 100)  // 2800W÷230V×sqrt(2) amplitude for E_I_AC_RMS_MAX_CNT samples; ((17.2÷√2)^2 × 0.1 Ohm)÷2 + 2Wswitching = 9.4W < 12Wdesign
#define E_I_AC_PULSE_MAX_AMP_10mA (19.1 * 100)  // 3100W÷230V×sqrt(2) amplitude for 1 sample
//#define E_I_AC_RMS_MAX_AMP_10mA (15.4 * 100)  // 2500W÷230V×sqrt(2) amplitude for E_I_AC_RMS_MAX_CNT samples
//#define E_I_AC_PULSE_MAX_AMP_10mA (17.2 * 100)  // 2800W÷230V×sqrt(2) amplitude for 1 sample -> triggered twice in 2 month with Pac=1800W
//#define E_I_AC_RMS_MAX_AMP_10mA (8.0 * 100)  // 1300W÷230V×sqrt(2) amplitude for E_I_AC_RMS_MAX_CNT samples -> triggered error even with 460W limit (11.03.2025 18:27)
//#define E_I_AC_PULSE_MAX_AMP_10mA (10.5 * 100)  // 1700W÷230V×sqrt(2) amplitude for 1 sample
#define E_I_AC_DC_OFFSET_MAX_10mA (0.8 * 100)  // 800mA in E_I_AC_DC_OFFSET_CYCLES consecutive 50Hz periods  todo decrease
#define E_I_AC_DC_OFFSET_CYCLES 8  // number of consecutive 50Hz periods for DC current fault

// todo: check if feedforward still causes i_ac 500mA 24kHz oscillation
#define PERMIL_V_DFFW_MIN  0  // 0% grid voltage direct feedforward, 100% PLL
//#define PERMIL_V_DFFW_MIN  200  // 20% grid voltage direct feedforward, 80% PLL; causes 25kHz 500mA i_ac when phase is not calibrated
//#define PERMIL_V_DFFW_MIN  500  // 50% grid voltage direct feedforward, 50% PLL; Test at 31Vac trafo did not cause LCL oscillation
//#define PERMIL_V_DFFW_MAX  500  // 50% maximum in case of high current due to distorted grid
#define PERMIL_V_DFFW_MAX  0
#define PERMIL_V_DFFW_INCR 60  // 60 equals 6% per control cycle -> 60% in 500µs
#define PERMIL_V_DFFW_DECR 1  // 1 equals 0.1% per control cycle; @70% direct feedforward, it takes 600*50µs=30ms to come back to 10%
// always 50% has higher inductor sound
// always 80% has even higher inductor sound

#define P_AC_MIN 0 // feed into grid only -> no AC2BAT for now
//#define P_AC_MAX ((5*32)/1.41) //113W  // todo implement anti windup in power controller regarding IAC_AMP_MAX_10mA
//#define P_AC_MAX (210)  // 210W minimum for energy packet controller
//#define P_AC_MAX (460)  // 460W for 2A Fuse
//#define P_AC_MAX (600)
//#define P_AC_MAX (1000)
//#define P_AC_MAX (1500)
//#define P_AC_MAX (1800)
#define P_AC_MAX (2000)
#define P_BAT_MIN_CHARGE 14  // BMS 4.7Watt; Final wiring: 6.9W including both contactors
#define P_MIN_PV2AC 18
#define P_MIN_HYBRID 25

/***************/
/* Fan control */
/***************/
#define FAN_P_AC_START 1200
#define FAN_P_AC_STOP 1000
#define FAN_RUNTIME_MINIMUM_SEC 30
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

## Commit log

2023-12-09 PCB production V1; pin planning complete
    [DCcurrent_sense.kicad_sch, Microcontroller.kicad_sch, PVBatteryInverter_Mainboard.kicad_pcb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]
2023-12-26 fixed some PCB components and added notes in schematic for PCB V2
    [Microcontroller.kicad_sch, PVBatteryInverter_Mainboard.kicad_pcb, PVBatteryInverter_Mainboard.kicad_sch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]
2023-12-26 tested CAN, PWM, UART, ADCs and all Sensors
2025-09-30 MPP Tracker tested with 19V supply 35W bulb as pre resistor; 32Ohm load resistor; 33kOhm Vdc sense
2025-09-30 tested AC control with 15V transformer, LCL filter and 4 Ohm series resistor; charging to 30Vdc successful
    [PVBatteryInverter_Mainboard.kicad_sch, VGRID.CSV]
2025-09-30 implemented battery CAN bus commands
2025-09-30 added watchdog; PV2AC with 10Watt at 48V
    [PVBatteryInverter_Mainboard.kicad_sch]
2025-09-30 without 5R6 AC precharge resistor; AC current 61mA offset; power consumption from DC and AC!
2025-09-30 PV boost auto switch to interleaved mode
2025-09-30 calib Vac and Vdc; implemented sml read -> tested in parallel with BMS and inverterdata output on same RS485 bus
2025-09-30 improved writing to monitor vars; grid voltage filter for matching amplitude; NO contactor or current feedforward
2025-09-30 monitor stream sync; MPPT too fast for grid control
    [ac_control.cpp, common.h, main.c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]
2025-09-30 fixed RC-lowpass freq
    [ac_grid.kicad_sch]
2025-09-30 PV battery charging and switch to PCC compensation tested
2025-09-30 improved battery_connected detection
2025-09-30 bootloader autostarts application if emergency button released at reset; RS485 update working
    [STM32_Bootloader.ioc, main.c]
2025-09-30 battery update request always triggers send_inverterdata
2025-09-30 bootloader RS485 init after Jump, otherwise Comm in App broken; reworked hybrid states
    [ac_control.cpp, common.h, main.c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]
2025-09-30 improved stability; optional print
    [ac_control.cpp, main.c]
2025-09-30 fixed mon_duty; fixed P_bat_const control; fixed AC turnoff during sunrise
    [ac_control.cpp, common.h, dc_control.cpp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]
2025-09-30 fixed gatedriver still disabled in PV2AC mode
    [ac_control.cpp]
2025-09-30 prevent short AC turnoff in the evening; improved battery handling and GMPPT
    [ac_control.cpp, dc_control.cpp, sys_mode_controller.cpp]
2025-09-30 fixed overvoltage error in transition from PV2AC to Hybrid mode
    [common.h, dc_control.cpp, sys_mode_controller.cpp]
2025-09-30 added errorcodes for battery; fixed unaligned access in sml_parser
    [STM32_PVBatteryInverter.ioc, ac_control.cpp, common.c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]
2025-09-30 reset microcontroller if battery switched off
    [sys_mode_controller.cpp]
2025-09-30 decreased PV start voltage; increased interval for RMS current fault
2025-09-30 charge Vcell to 3.50V instead of 3.56V added dynamic shift to direct voltage feedforward added grid voltage and freq error codes added external Pac control fixed power direction: grid to battery
    [ac_control.cpp, common.c, common.h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]
2025-09-30 updated BMS struct (Kalman SoC and cycle counter)
2025-09-30 fixed battery_almost_full condition
2025-09-30 switched RS485 text parameter interface to Modbus; reset hybrid mode if main mode is changed
    [ac_control.cpp, dc_control.cpp, main.c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]
2025-09-30 reset Modbus after SML cycle (each second); update BMS lib
    [main.c]
2025-09-30 shutdown of already discharged battery when PV power is low
2025-09-30 increased minimum battery cell voltage and prevent early battery shutdown to prevent BMS DEVICE_XREADY fault
    [sys_mode_controller.cpp]
2025-09-30 Battery Supervisor Board: CAN Bus RX test
2025-09-30 HV Vbat measurement circuit for PE connected microcontroller
2025-09-30 switched bootloader to internal oscillator
    [STM32_Bootloader.ioc, main.c]
2025-09-30 fixed battery config; increased switching frequency to 40kHz, control still at 20kHz; tested voltage sensors and overcurrent Analog ADC watchdog
    [STM32_BatterySupervisor.ioc, common.h, dc_control.cpp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]
2025-09-30 5 minute charging test passed, using isolated AC-rectifier + 2x75W lightbulb as PV emulator; Test end with BMS unplug causing watchdog reset
    [common.c, common.h, dc_control.cpp]
2025-09-30 Battery_Supervisor: fixed voltage measurement circuit
    [PVBatteryInverter_Mainboard.kicad_sch]
2025-09-30 5 minute charging test passed using both PCBs; added shared code folder
2025-09-30 transmit battery current from Supervisor to Inverter
2025-09-30 Added GPIO interrupts for current sensor fault signals. Tested with Supervisor PCB and 60A AC pulse. Added GPIO interrupts for overtemperature. Tested with 1kOhm instead of NTC.
2025-09-30 Fixed overtemperature signal with 10nF. Added Kalman filter for SoC. Tested modbus registers for cell voltages. 15min 31W charging test passed.
    [PVBatteryInverter_Mainboard.kicad_sch]
2025-09-30 test with 320V DC and 33V AC RMS passed
2025-09-30 added 5V supply undervoltage detection to protect GaN from low gatevoltage. Tested trigger at ~4.65V.
    [PVBatteryInverter_Mainboard.kicad_sch, PVinverterCALC.ods]
2025-09-30 added nonlinear inductor model which was used in 48V system; remanent model is in rp-tfm repo
2025-09-30 31Vac 3.1Arms current test; 320Vdc
2025-09-30 230V AC grid with 30mA RCD and 2x1kW debug resistance: idle power ~3W, 15VA; disabled energy packet controller; avoid frequent contactor actions in case of grid voltage drop during contactor close; s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
    [PVinverterCALC.ods]
2025-09-30 tested direct 230V AC grid with 30mA RCD; power meter: 2.6-5.2W, 80VA
2025-09-30 tested direct 230V AC grid with 10mA RCD
2025-09-30 added fan control
    [PVBatteryInverter_Mainboard.kicad_sch]
2025-09-30 improved UART monitoring
2025-09-30 ISR reordered to avoid noise of ADC2 disturbing ADC1; only one ADC should run at the same time; added second ISR debug pin; 8x oversampling for ADC1
    [PVBatteryInverter_Mainboard.kicad_sch, ac_grid.kicad_sch]
2025-09-30 enabled and tested analog watchdog for AC current
2025-09-30 trigger ADC before CNT_MAX; checked ac duty calc duration max 5.1+18.4 = 23.5us < 25us
2025-09-30 fixed PI controller saturation behaviour; calib Vac offset with 325V sine; tuned PLL phase shift
    [PVinverterCALC.ods]
2025-09-30 garage charging test with PV emulator 2x75W
2025-09-30 fixed sporadically read of 4 cell voltages as 0V
2025-09-30 fixed sporadically read of temperatures as 0; fixed battery current limit; increased AC power to 460W
    [config.h, main.c]
2025-09-30 added battery PCB temperature; improved AC charging; adjusted battery temperature limits
    [PVBatteryInverter_Mainboard.kicad_sch]
2025-09-30 fixed external power immediate reset to 0; fixed PI-controller saturation
    [sys_mode_controller.cpp]
2025-09-30 improved AC charging; increased AC current; scaled p_ac; increased min cell voltage; decreased cell imbalance limit; use modbus SoC limits
2025-09-30 BMS improvements; changed default PV boost stage, because stage 1 needs repair; turnoff AC if Vbat < Vgrid"
2025-09-30 prevent boost stage non sensed overcurrent due to high PV boost ratio or rapid change
    [dc_control.cpp, main.c]
2025-09-30 prevent bms power turnon without sufficient v_dc; BMS lib: improved CAN rx using multiple filters
    [STM32_PVBatteryInverter.ioc, can_bus.c, dc_control.cpp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]
2025-09-30 battery supervisor: improved CAN robustness; green LED shows contactor status
2025-09-30 reduced max battery temperature limit; error turns BMS 12V off; added p_ac controller; reduced limit for interleaved DCDC mode
    [ac_control.cpp, dc_control.cpp]
2025-09-30 increased AC current and error limit; increased min PV power; fixed BMS turnoff
    [config.h]
2025-09-30 fixed PV low power cnt
    [sys_mode_controller.cpp]
2025-09-30 modbus reg for AC low power packet mode
    [PVinverterCALC.ods]
2025-09-30 increased minimum cell voltage to avoid imbalance; increased AC power
    [config.h, sys_mode_controller.cpp]
2025-09-30 improved modbus write register (clamp before write); increased default minimum SoC
2025-09-30 increased AC power; battery i_discharge_max = 6A
2025-09-30 increased AC power to 1.5kW; increased BatterySupervisor pulse current limit from 10A to 15A; use advanced battery model for SoC estimation
2025-09-30 improved battery model: lower resistance; higher weight for coulomb counting
2025-09-30 increased AC power; added Modbus p_pcc_ref; added bat current limits for fault condition
2025-09-30 increased AC current error condition
    [config.h]
2025-09-30 improved behaviour with empty battery; lowered max cell temp limit
2025-09-30 allow error reset after 30 seconds; improved PV2AC state switch; increased Pac and Iac_pulse_max; new MPPT: v_pv instead of dutycycle
    [config.h, dc_control.cpp, sys_mode_controller.cpp]
2025-11-22 fixed v_pv calculation; use PV2AC mode in the morning if p_pcc > 20W
    [ac_control.cpp, common.h, config.h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]
2025-11-30 fixed mode change; pv_power: calc RC lowpass; compensate DC link capacitor
    [PVBatteryInverter_Mainboard.kicad_sch]
2025-12-15 added mode transition PV2AC to OFF in case of empty battery; improved PV2AC mode change; fixed voltage deviation error during battery turnoff
    [config.h, dc_control.cpp, sys_mode_controller.cpp]
2026-02-28 reduced AC power to 1kW, which minimized AC current errors; started in december 2025, used until 28.2.2026
2026-03-02 added monitor variable ctrl_mode_AC; increased AC current
2026-03-04 modbus reg to disable use of battery; respect modbus SoC limit; limit MPPT power if required
2026-05-18 added manual sensor calibration mode and PWM test mode
2026-05-21 use excess PV power for battery charging and ignore EMS charging power limit
2026-05-22 single boost converter stage
2026-06-13 preserve WatchdogRST flag in bootloader; check ISR runtime; check GaN reverse conduction (prevent system operation without active boost converter in case of high PV input current, which could damage 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
    [common.c, common.h, config.h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]
2026-06-29 increased max voltage and current
2026-06-30 fixed AC gatedriver pulse active because of PV power measurement noise; update Readme.md
    [sys_mode_controller.cpp]

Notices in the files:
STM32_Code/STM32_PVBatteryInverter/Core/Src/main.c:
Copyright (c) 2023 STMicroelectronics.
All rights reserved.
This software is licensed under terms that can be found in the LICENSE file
